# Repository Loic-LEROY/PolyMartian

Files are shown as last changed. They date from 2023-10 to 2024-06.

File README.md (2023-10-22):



## Objectives
The purpose of the robot is to carry out several tasks in complete autonomy. The tasks to be performed are as follows:
- Pick up different types of plant

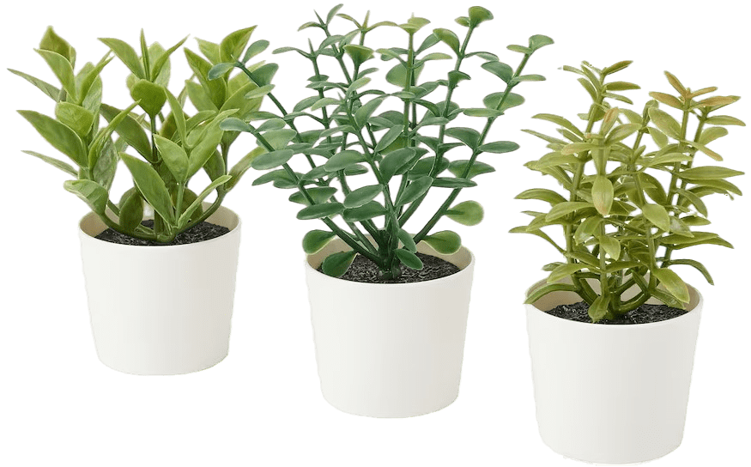
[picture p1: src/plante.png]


- Place plants in pots

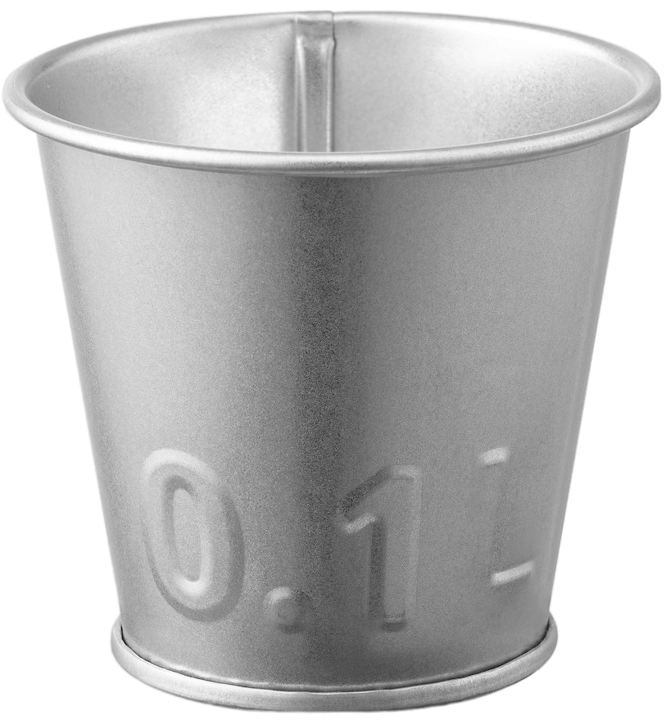
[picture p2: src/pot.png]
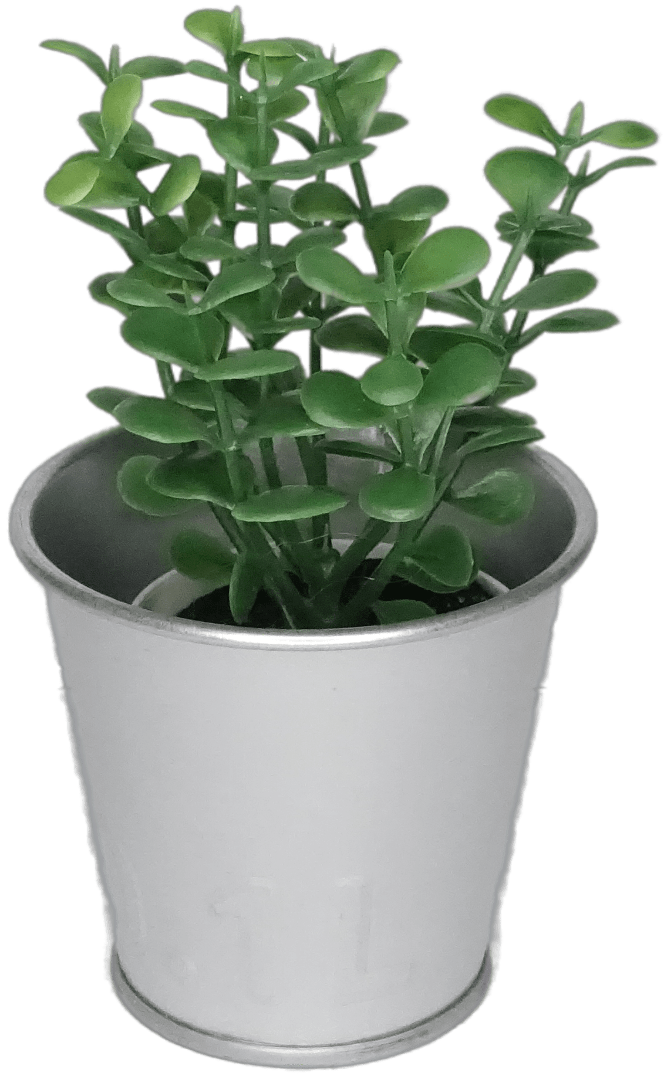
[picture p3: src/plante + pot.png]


- Bring plants to a predefined area

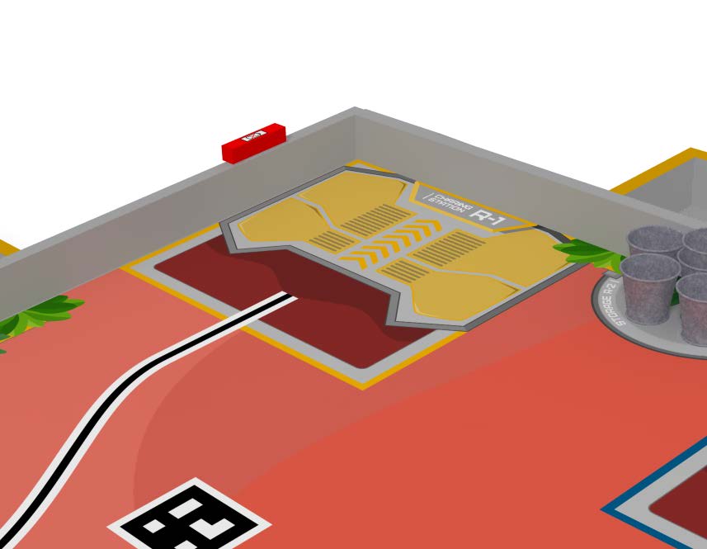
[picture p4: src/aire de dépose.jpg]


- Sort plants by type

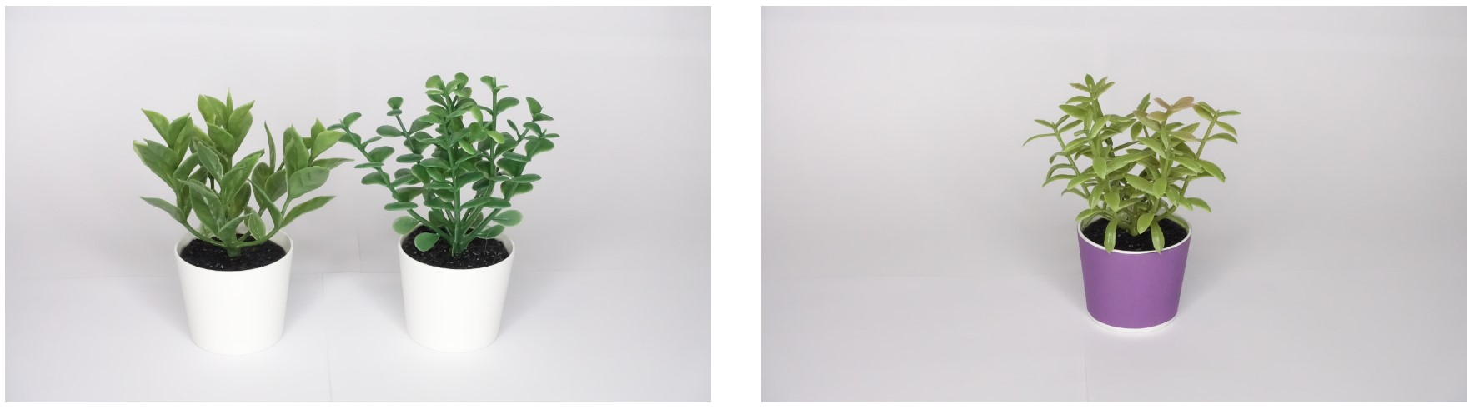
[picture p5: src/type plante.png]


> Two fragile plants, one resistant plant

- Orienting solar panels

All the work must be completed within the allotted time and without colliding with the environment (walls, other robots, plants, pots).

## constraints
- Robot dimensions :
    - Perimeter between 1200 and 1300 mm

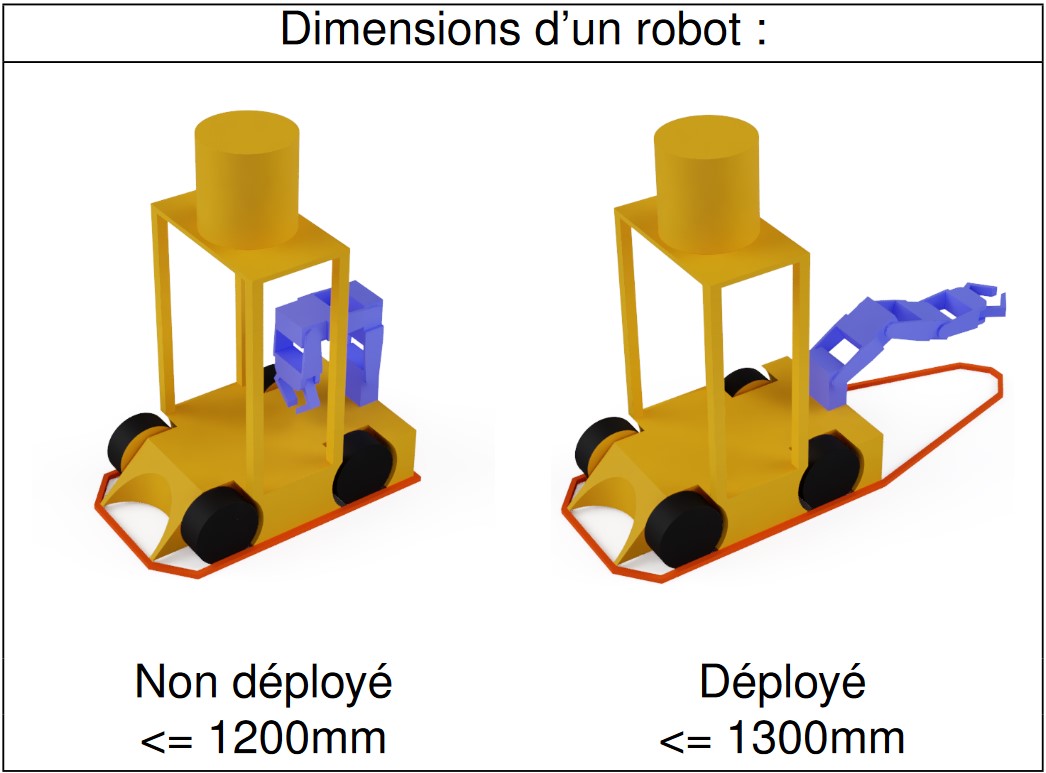
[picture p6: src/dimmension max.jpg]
    
    
    - Height under 350 mm

## Main components
- Chassis / Rolling base
- Gripper system (rail-mounted gripper)
- Vision systems (cameras, sensors)
- Storage system (turntable)

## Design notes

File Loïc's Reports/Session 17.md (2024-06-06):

# April 16, 2024
## Emergency Switch
During this session, I mounted the emergency switch to the robot. I placed it on the most accessible area possible, so that it can be easily reached in case of an emergency. I also connected the switch to the robot's power supply, so that it can cut off the power in case of an emergency. I tested the switch to make sure it works properly, and it does. The robot is now equipped with an emergency switch, which will enhance its safety features so we will be able to homologate it.



> The emergency switch mounted on the robot.

## Ultrasonic Sensors
Also, I mounted the ultrasonic sensors on the robot. I placed them on the top platform of the robot, facing forward and backward. I connected the sensors to the robot's main board, and tested them to make sure they work properly. The sensors are now ready to be used for obstacle detection and avoidance. This feature is essential for the robot to be able to participate in the competition.

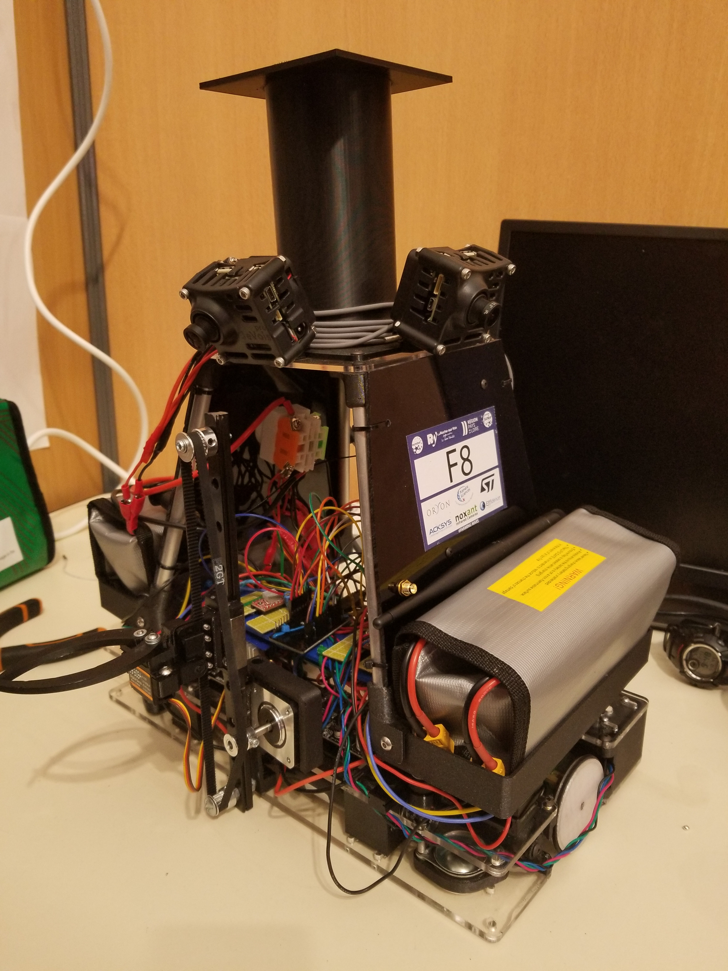
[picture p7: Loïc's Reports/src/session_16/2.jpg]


## Beacon mast
Finally, I mounted the beacon mast on the robot. I placed it on the top platform of the robot, so that it can be easily seen from a distance.



## Next session
- Participate in the competition.

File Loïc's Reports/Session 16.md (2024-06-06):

# April 09, 2024
## Cameras mouting system
To mount the cameras on the platform, I designed a mounting system that allows to easily adjust the angle of the cameras. The system is composed of a 3D printed part that can be attached to the platform using fou M4 screws. Then, a small part must be glued on the camera fan to attach it to the 3D printed part. The camera can be rotated and tilted to adjust the angle. The system is working well and the cameras are now mounted on the platform.

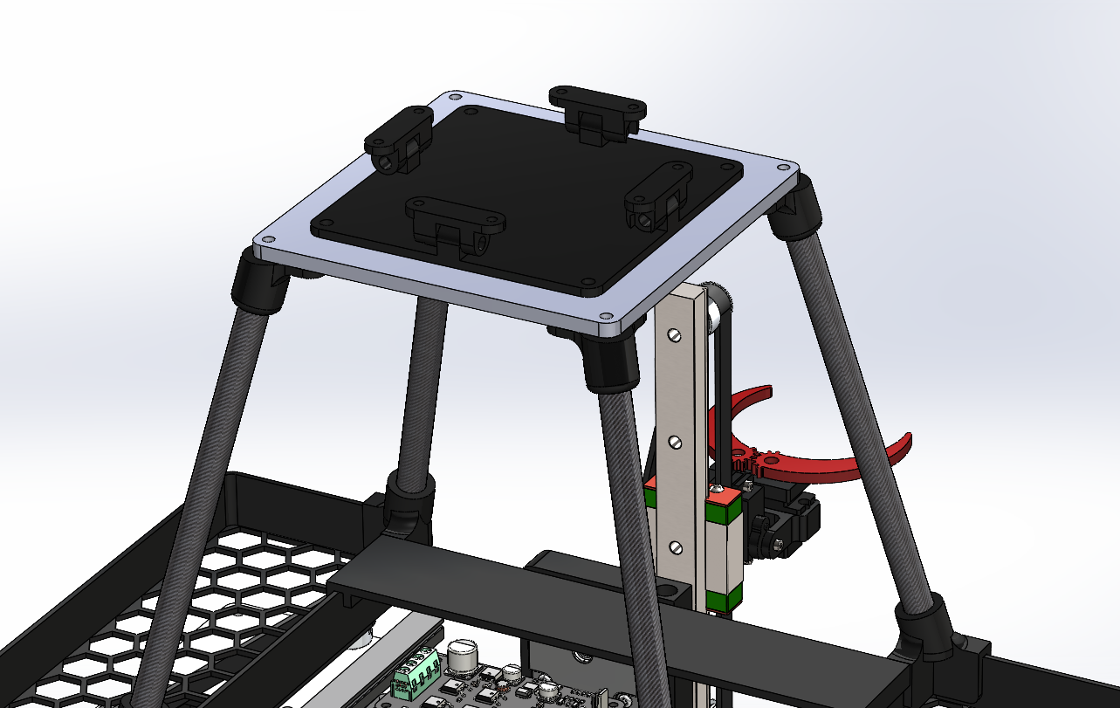
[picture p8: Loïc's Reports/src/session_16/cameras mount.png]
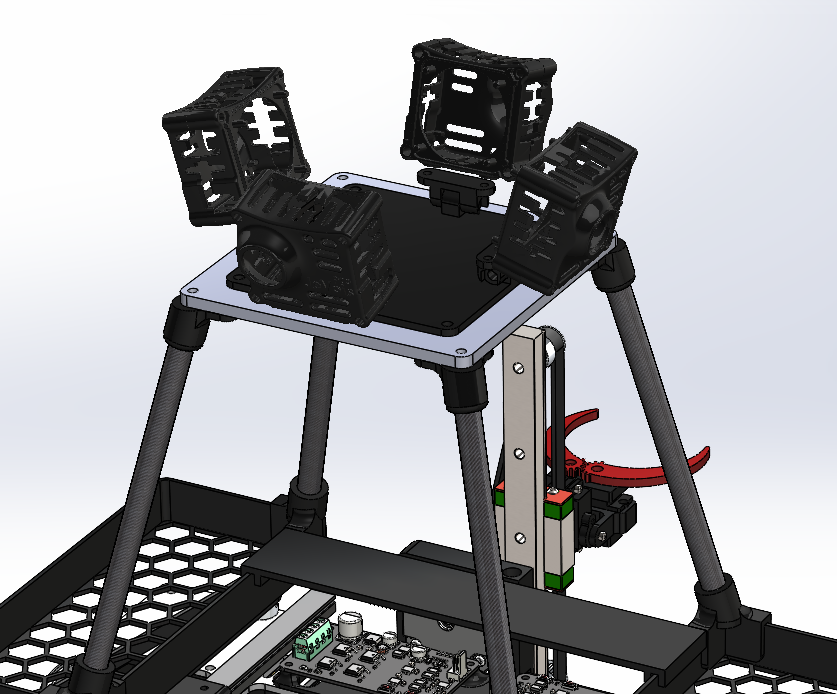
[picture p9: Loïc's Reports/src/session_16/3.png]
 

> The camera mounting system in SolidWorks



> The camera mounting system for real

## Next session
- Assemble the emergency stop button
- Design the beacon mast

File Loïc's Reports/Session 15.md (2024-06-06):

# April 02, 2024
## Cameras mounting platform
The cameras mounting platform is attached on top of the rolling base of the robot. It is composed of four aluminum tubes that are attached to the base with a 3D printed part. The platform is scarre and measures 120mm. Before laser cutting the platform itself in acrylic glass, I made one using cardboard to make sure the dimensions were correct. The platform is attached to the tubes with 3D printed parts and screws. 

<div align="center">
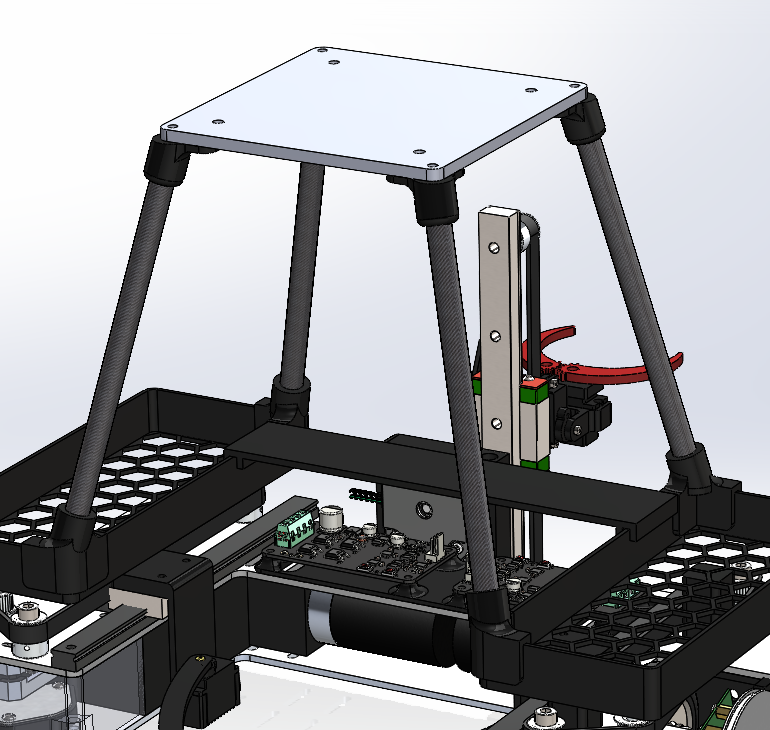
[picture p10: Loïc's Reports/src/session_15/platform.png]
    

    The platform on the robot
</div>

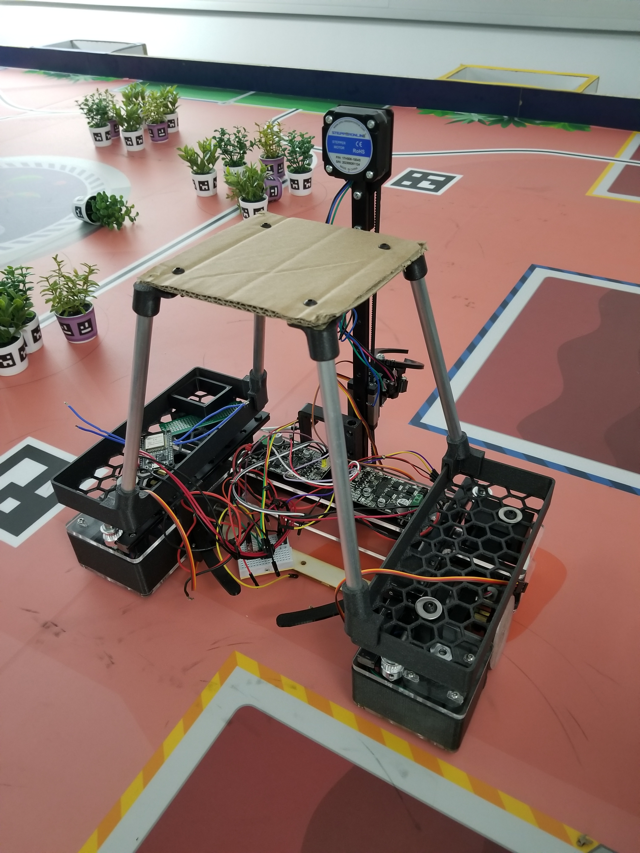
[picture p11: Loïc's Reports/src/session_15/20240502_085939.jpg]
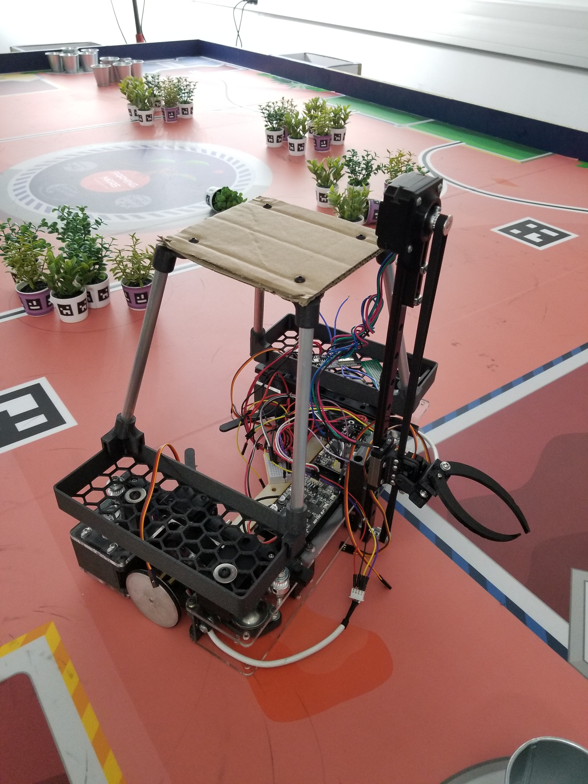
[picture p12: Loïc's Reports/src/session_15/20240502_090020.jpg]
  

> The cardborad prototype.

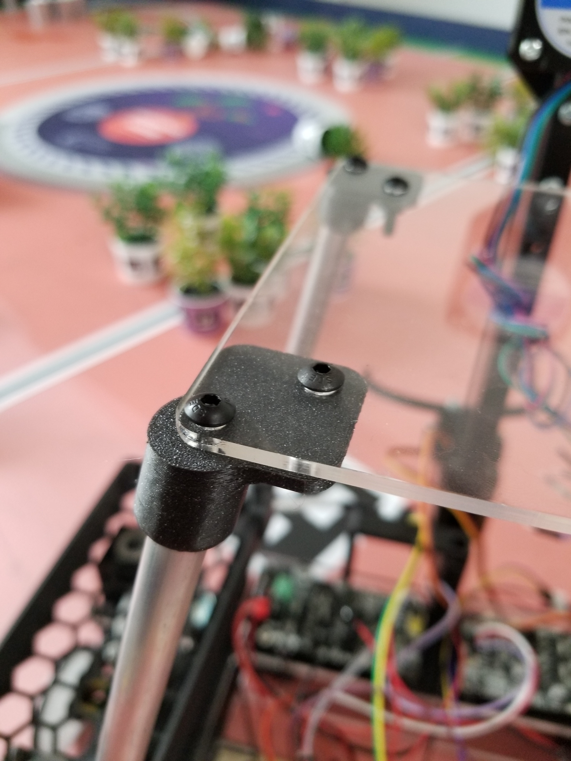
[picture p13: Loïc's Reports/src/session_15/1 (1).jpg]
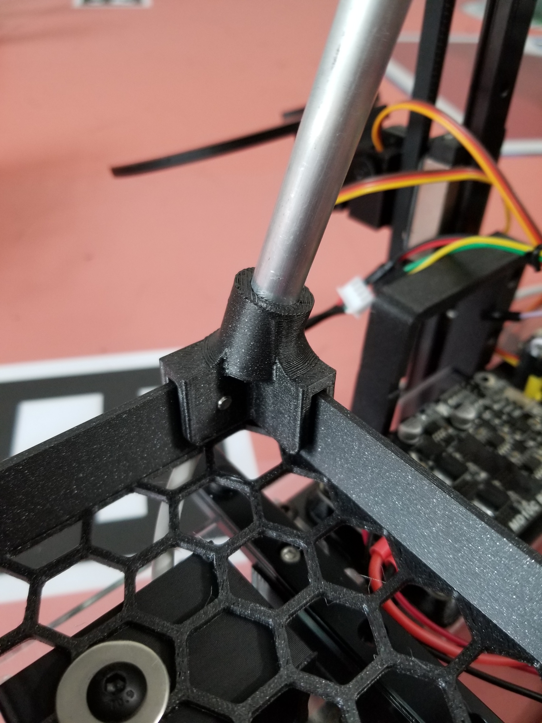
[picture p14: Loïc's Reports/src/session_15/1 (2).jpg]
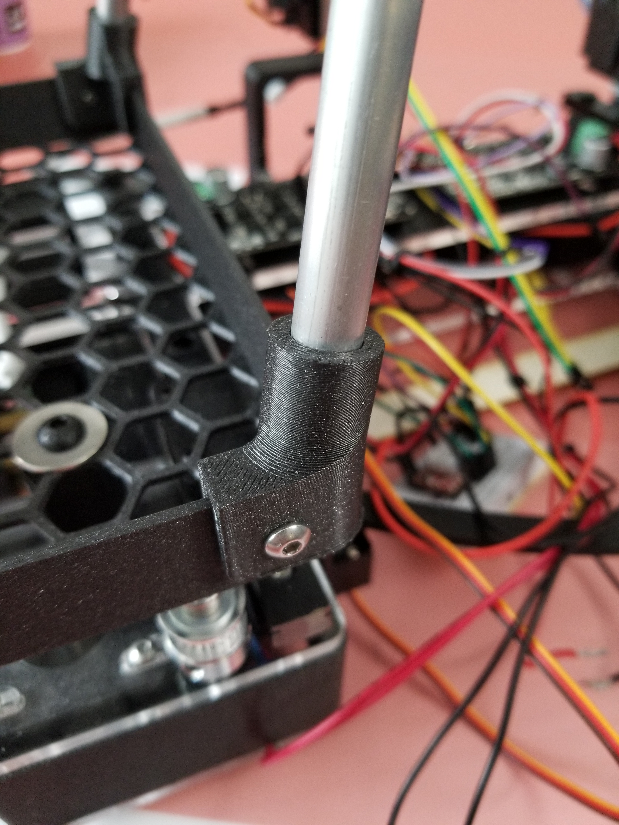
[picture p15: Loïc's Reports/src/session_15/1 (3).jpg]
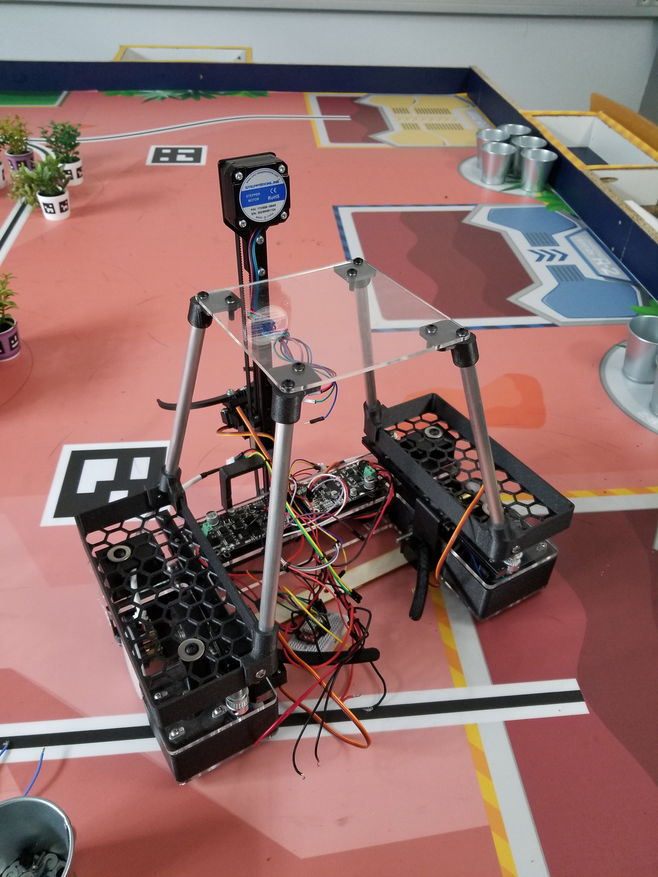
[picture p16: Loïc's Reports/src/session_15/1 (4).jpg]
   

> The 3D printed parts and the plexiglass platform.

## Next session
Next session, I will work on the cameras mounting system.

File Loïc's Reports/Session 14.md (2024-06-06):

# March 29, 2024
## Battery rack
In order to mount the batteries on the robot, I designed two "baskets" that will hold the batteries on both sides of the robot. The baskets are 3D printed in PETG for strength and durability. The bottom of the baskets have a honeycomb hole patern to lighten the weight of these parts. The batteries are held in place by a strap that goes around the battery and through the basket. The baskets are mounted on the robot using two M4 screws. Between the baskets and the robots, there are 3D printed spacers so the horizontal linear actuators can operate under them. 

On one side of the robot, the batteries are connected in series to provide 24V to it (2*3S = 24v). On the other side, only one battery is connected to provide 12V to the cameras.

<div align="center">
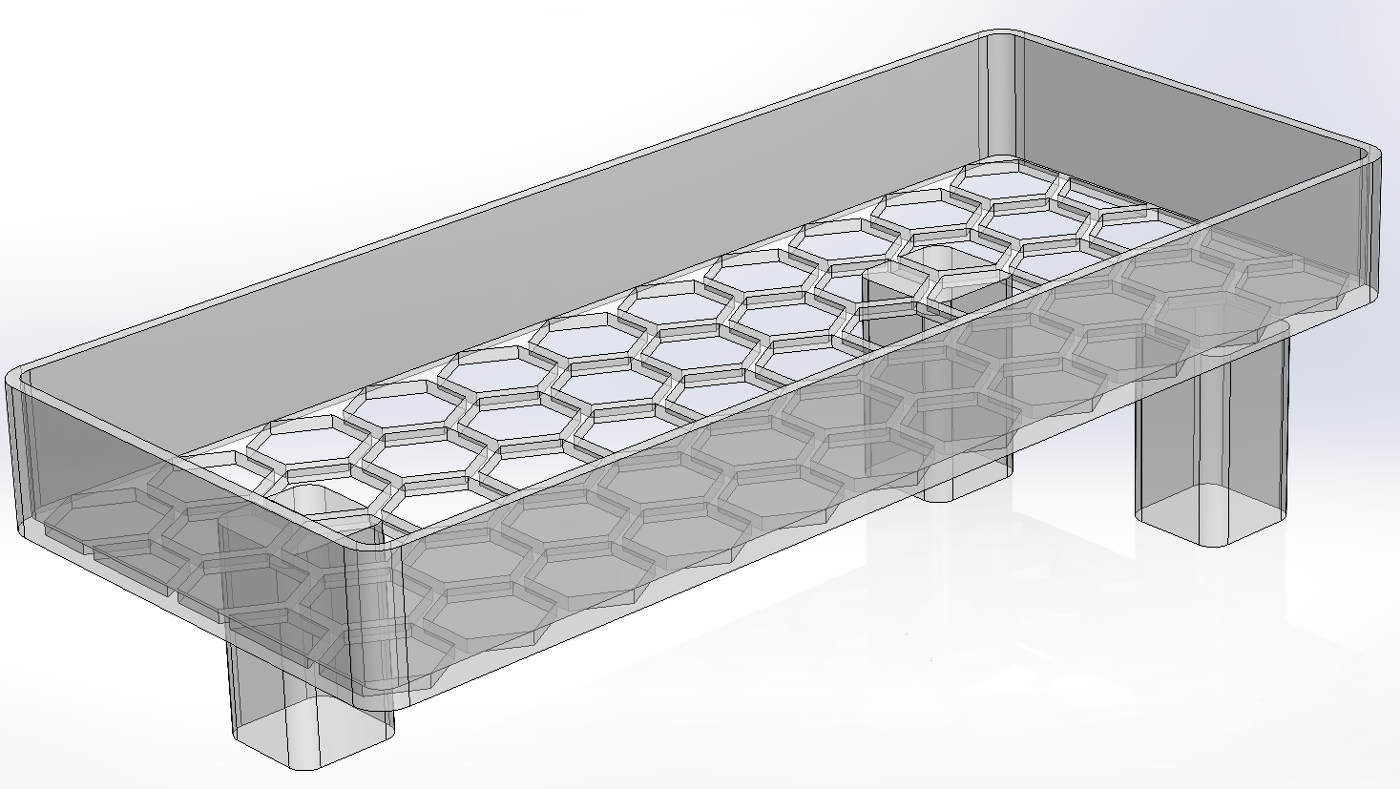
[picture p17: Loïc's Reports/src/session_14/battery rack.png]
    

    A battery rack
</div>
<div align="center">
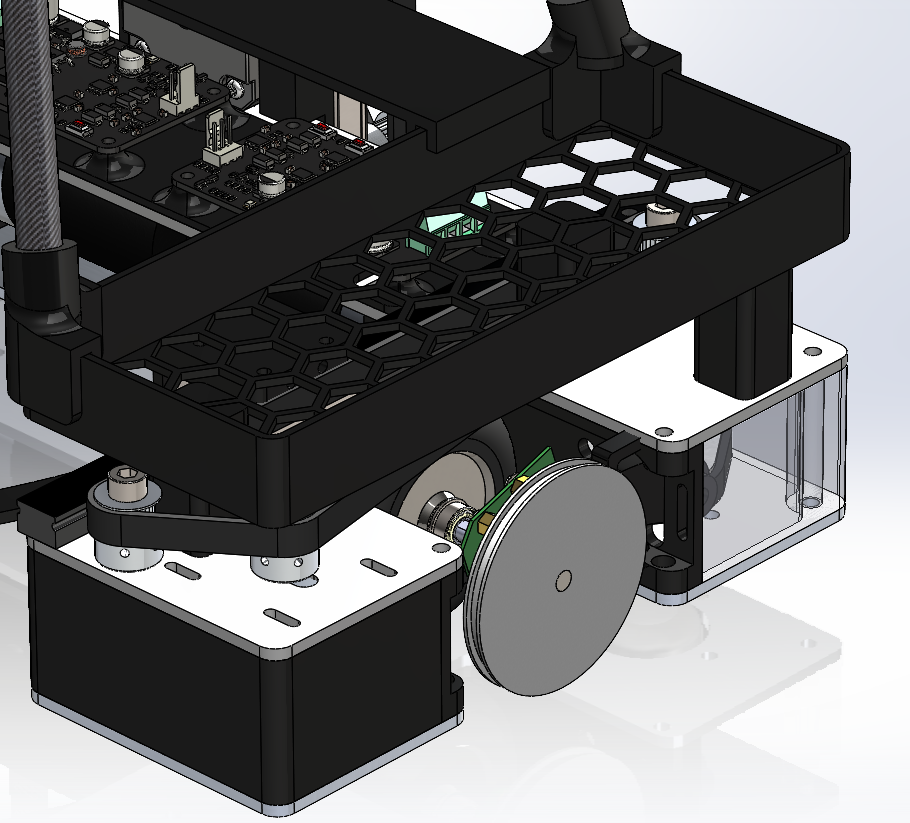
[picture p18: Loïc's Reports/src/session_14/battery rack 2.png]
    

    A mounted battery rack
</div>

## Mounting for electronics
I designed a mounting plate for the electronics that will be mounted on the robot. The plate is 3D printed in PETG. The electronics are mounted on the plate using zip ties. The plate is mounted on the robot's battries racks using super glue.

<div align="center">
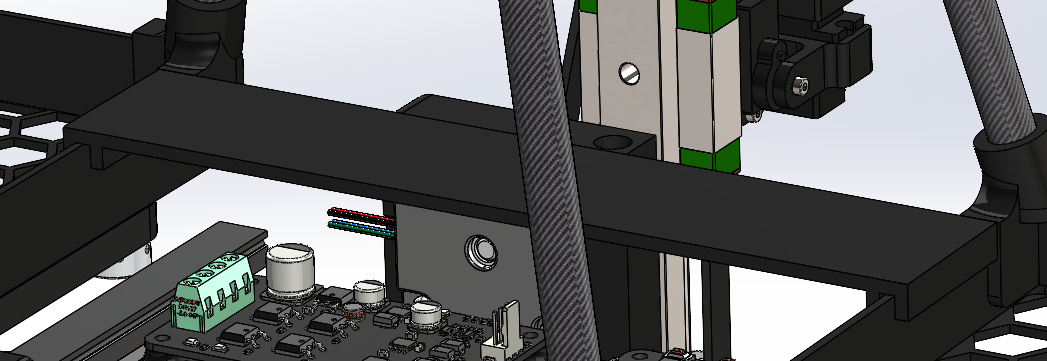
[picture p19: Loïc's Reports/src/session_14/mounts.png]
    

    Electronics mounting plate
</div>

### Next session
- Mount the electronics on the robot
- Connect the batteries to the robot
- Designed the cameras mounting system

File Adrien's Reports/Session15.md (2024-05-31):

# Session report 15: March 29, 2024

**Session objective:** Enable 2 movements trajectory to reach any coordinates on the playfield. Switch from an Arduino to an ESP32 on the robot. Find new lenses for our cameras.

## Finding new lenses for our cameras
One of the main problems at Eurobot's competition, is wifi waves interferences. So we were worried about positionning a camera on the calculation zone support, cause our communications would be easily disrupted or delayed. As our cameras are the main sensors of the robot, we decided for safety reasons to put all of  them on the robot. But the lenses provided with JevoisPro cameras have an angle near 60° so even with our 4 cameras we wouldn't be able to cover 360°.

To solve this, we decided to change our lenses for fish eyes ones which deform the image to allow huge angles sight. We chose 120° wide angle lenses to have redundancy as our cameras will be tilted towards.

## Take in hand the ESP32 chip to replace our Arduino Mega with a more powerful chip

I chosed to replace the Arduino Mega for an ESP32 for many reasons : 
- ESP32 has a higher clock speed, up to 240Mhz compared to 16 MHz for the Arduino Mega, so we will be able to have a higher sampling frequency.
- It can process to multiple tasks at the same time (for example to deploy an actuator while moving).
- It has WIFI and Bluetooth integrated, so it will be easier to send commands to configure it before making it fully autonomous.

First, we need to install the USB driver, its name can be easily identified on windows device manager and then we can downloaded from internet.
I wanted to be able to programm it with Arduino IDE, so to be able to do this, i searched for ESP32 board package by Espressif in the arduino software. 
Finally with both package and driver installed, we can easily upload code to it by selectionning the board and COM port in the Arduino menu.
Be awared that it's only possible to upload a code on it while it's in boot mode. So, to exit boot mode, on some ESP32, you need to press the boot button for few seconds while the programm is being uploaded.

## Recalibrate the robot's odometry
As a new version of the rolling base has been assembled, i had to recalibrate the odometry to be able to continue working on the displacements algorithm. To do this, i first recalibrated the robot for rotations, by reading the values from each encoder after manually doing a 360° rotation around a nail (thanks to a wood calibration part temporarily fixed on the robot which has an hole at the cinematic center of the robot). 
Ad then calibrate linear odometry by moving the robot in straight line (by pushing it forward leaning it against a wall) and reading both the values of the encoders and the distance travelled on a rule.

Linear calibration : 

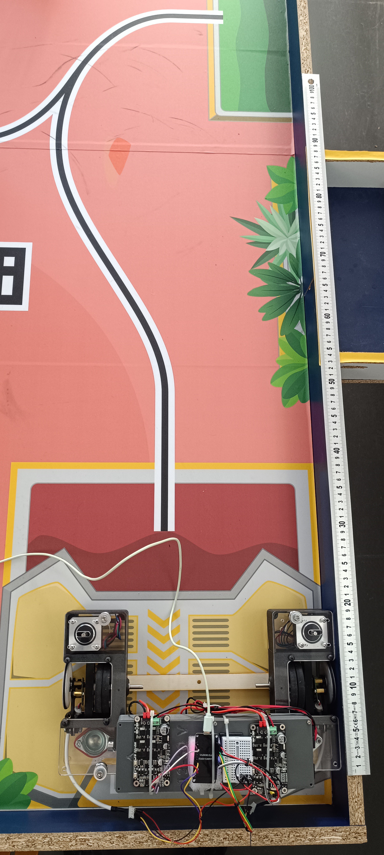
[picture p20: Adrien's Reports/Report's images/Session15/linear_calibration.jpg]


## Next session tasks
Finalize adjusting the current Arduino code to ESP32 by adding an interruption to replace millis() used for sampling. Find correct PID coefficients. Work on data transfer between ESP32 and the Jetson Nano, and between the Jetson Nano and our four cameras.

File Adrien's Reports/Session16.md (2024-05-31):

# Session report 16: April 9, 2024

**Session objective:** Switch from the Arduino Mega to an ESP32 on the robot. Etablish a connection between the Nvidia Jetson and the cameras. Optimize the closed loop control algorithm by setting a timer on the ESP32 to sample.

## Communication in USB between our cameras and the Nvidia Jetson
The first step to use our cameras on our robot was to etablish a connection between our four cameras and the Nvidia Jetson so we are able to send commands to the cameras to configure them and overall receive their processed data. As the Jetson has four usb ports, it was easier 

I then followed a tutorial written by Jevois, the manufactrer of our cameras : http://jevois.org/doc/USBserialLinux.html
To connect a camera to the Linux host provided on the Jetson using serial-over-USB, i first identified the device's port used by the camera with the command ```dmesg``` or ```lsusb```. Then i added permissions by adding my user profile to the dialout group with the command ```sudo usermod -aG dialout $USER$```. To avoid interference from the ModemManager program, which probes new serial devices, i also disabled the ModemManager  ```sudo killall ModemManager```. Then i was able to use serial communication with the application ```minicom``` (after installing it with ```pip install minicom```) and send configurations instructions to the camera.

## Problem with serial communication with ESP32
After successfully transfering a program to the ESP32, it was constantly rebooting as the following message was continously printed on the console : 

rst:0x8 (TG1WDT_SYS_RESET),boot:0x13 (SPI_FAST_FLASH_BOOT)
configsip: 0, SPIWP:0xee
clk_drv:0x00,q_drv:0x00,d_drv:0x00,cs0_drv:0x00,hd_drv:0x00,wp_drv:0x00
mode:DIO, clock div:1
load:0x3fff0030,len:1344
load:0x40078000,len:13516
load:0x40080400,len:3604
entry 0x400805f0
ets Apr 9 2024 09:22:53

After some researchs i found out that on a classic ESP32 there are 6 pins which are used by internal Flash and thus musn't be connected to anything otherwise the chip will reboot indefinitely. The problem was simply solved by switching the cables on other pins, not used by internal flash, based on the following ESP32 Pinout diagramm made by uPesy : 
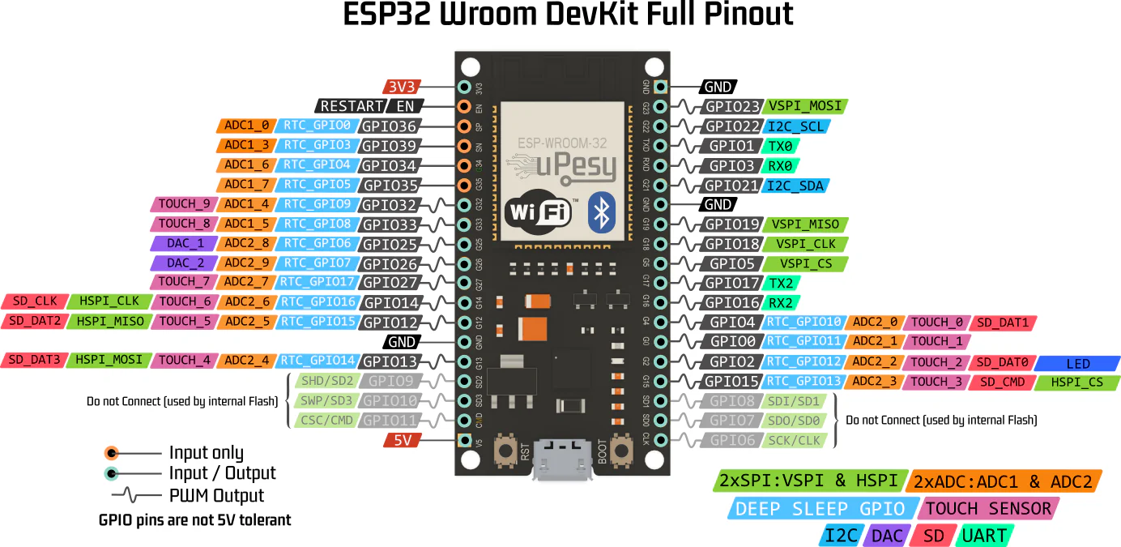
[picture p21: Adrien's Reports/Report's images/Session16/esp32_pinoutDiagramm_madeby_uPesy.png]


## Test of an encoder with ESP32
Then I wired an Encoder to the ESP32 to verify it is still working as ESP32 works only with 3.3V signals so it may be incompatible with some numerical devices if they threashold is superior at 3.3V.
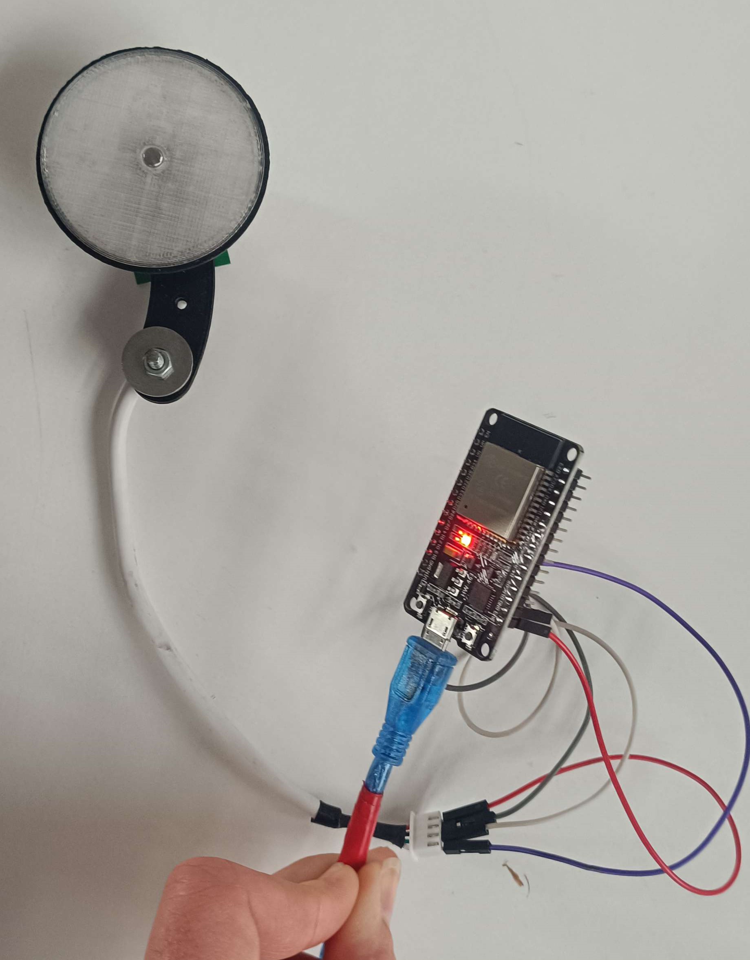
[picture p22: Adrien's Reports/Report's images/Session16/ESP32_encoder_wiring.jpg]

But hopefully communications between our encoder and the esp32 worked perfectly so it wasn't necessary to use a logic level shifting chip.

## Temporary wiring
Then i wired cables on the final version of our robot. This wiring is still temporary and will be used to do tests on the robot without waiting for all cables to be welded correctly. This will also prevent bad suprises, cause we will be sure that our wiring is correct before welding cables.

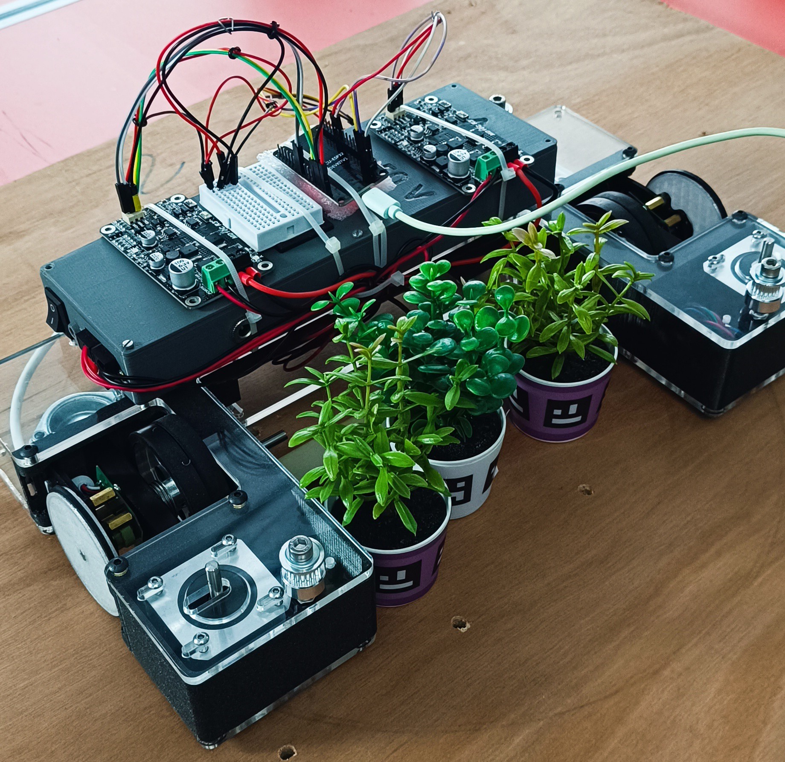
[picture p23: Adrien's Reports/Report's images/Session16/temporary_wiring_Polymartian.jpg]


## Next session tasks
We have finally received all the components to be able to assemble the final version of the robot, so next session should be fully consacred to the calibration of the PID and optimizing the robot's displacements. Finally i will implement curved trajectories which will be necessary to avoid obstacles properly without loosing too much time.

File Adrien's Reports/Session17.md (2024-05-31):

# Session report 17: April 16, 2024

**Session objective:** Create the wiring diagram of our main robot, wire cables on the final version of our robot, add programm actuators sequences.

## Wiring diagram
First, as during the competition we will probably need to do maintainance on the robot, to avoid loosing time with wiring, I created a wiring diagram on the software Fritzing. Older versions of this software can be downloaded for free here : arduinofactory.fr/telecharger-fritzing-gratuitement-et-legalement.
This diagramm will also be used by Teo Baillot, a member of the team who is in charge of the cable management of the robot and who will weld cables on the final version to avoid having cables unplugging on the robot during a match.

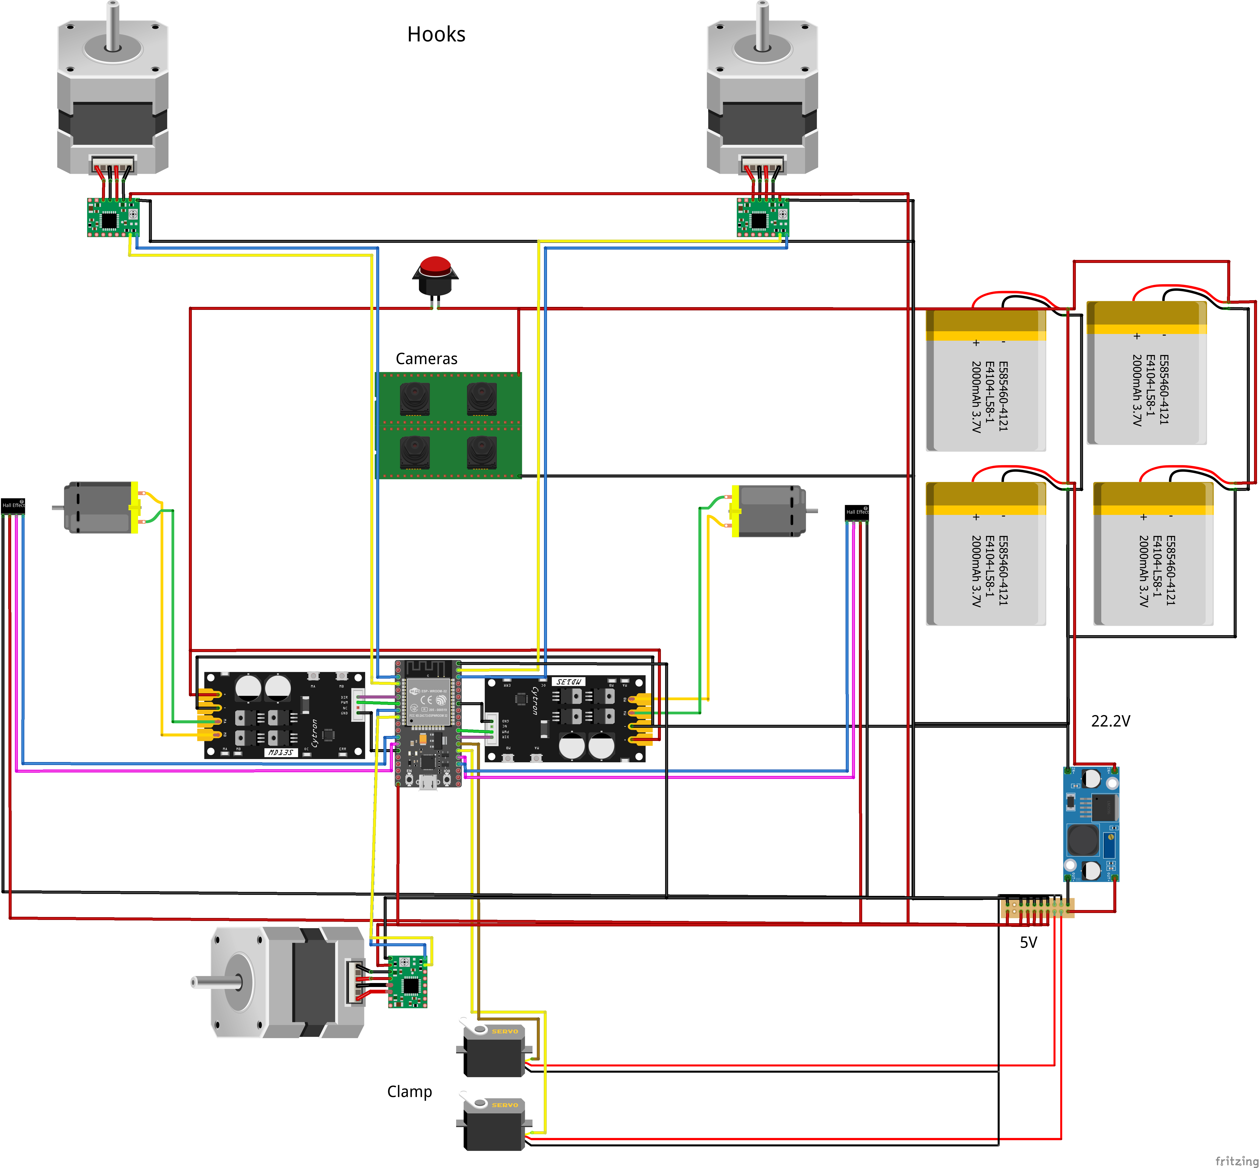
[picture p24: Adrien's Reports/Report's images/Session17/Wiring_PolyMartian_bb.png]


Two Lipos batteries are 3s 35C 2200mAh. 3S means the battery is made with 3 cells, so as each cell provides 3.7V, a 3S battery provides a voltage of 3*3.7V = 11.1V. So we put two batteries in serie to obtain a voltage around 22V which is perfect for our DC motors. 
We decided to put two more Lipos in parallel as we want to be sure that we will have enough capacity and so if we have a problem with a pair of batteries the robot will be able to continue his work with the others two batteries.

An emergency stop button is directly wired between the Lipos and the motors to be able to stop the robot at any time if a problem occurs during the competition.

## Wiring on the robot
To avoid cables disconnecting during the competition, it was indispensable to weld all cables. Even with 2 people welding cables simunlateously, it took multiple hours as the connexions on the esp32 are really thin and as we had only 0.75mm² cable. Hopefully, we made the good decision to buy silicone cables which are really convenient to weld cause they are very flexible and overall heat resistant.

But after that, we still needed to do some modifications on the robot or to modify wiring, and this experience showed us that wiring cables on a project which is aimed to be constantly modified was not the best solution. Thus, next year we will try to create our own cards with connectors for flat cables which are really convenient to disconect and reconnect and also very strong.

## ESP32 driver not foundable
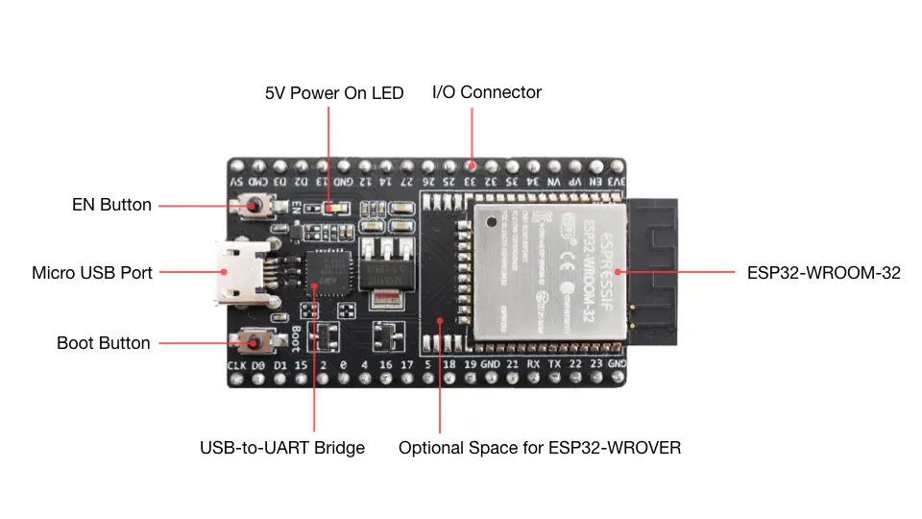
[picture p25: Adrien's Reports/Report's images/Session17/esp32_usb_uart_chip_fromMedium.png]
One of our spare ESP32 wasn't recognized by my computer. I spent almost one hour searching for this driver and testing different ones who had the same reference indicated in the device manager or also by identifying the name of the USB to serial converter chip on the ESP32 (see infography below from Medium.com) 
Our ESP32 was a copy from the original, and as i found no driver compatible with it, i wasn't able to make it work so i had to switch for another esp to not loose too much time.

## Wheel friction and weight repartition problem
Finally, now that the wiring was finished, i wanted to test the new rolling base with my closed loop control algorithm made previously but a problem occured. A wheel had too much friction compared to the other leading to bad trajectories. This was due to a free wheel which had friction with motor shaft.
The left wheel didn't grip correctly to the ground caused the inacurracy of some 3d printed part on the robot or its deformation. But this error is so small that it should be corrected when we will put weight on the robot with our batteries. Meanwhile, we can add counterweights on the robot to replace the future batteries.

## Next session tasks
Finalize the code of the robot to be ready for the robotics cup which will happen from 8th to 11th May 2024.

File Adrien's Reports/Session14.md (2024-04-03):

# Session report 14: March 29, 2024

**Session objective:** Implement new speed PID corrections where the error is the difference between the estimated speed (which is this time calculated from a trapezoidal or triangular speed profile based on the position to be reached) and the actual speed of the robot.

## Reminder

During the previous sessions, I had written a function get_phases_distance() capable of estimating the duration of each phase (acceleration, constant speed, deceleration) needed to reach a specified distance, and another function get_speed_target() capable of determining the speed target to be reached at each instant based on this speed profile.

## Resolved issue with get_speed_target()
The function worked by comparing the remaining distance to travel with the distances needed to accomplish acceleration and deceleration phases to determine when to switch to the next phase. Each time it was invoked (based on sampling frequency), it incremented the speed target by either max_acceleration or max_deceleration, depending on the current phase.

However, this approach didn't work properly because there was no correlation between the sampling frequency at which acceleration was added and the distance traveled.

To address this issue, I modified the function to be based on phase durations rather than phase distances. For instance, the duration of the acceleration phase represents the number of times we need to increment the speed target by the max_acceleration coefficient to reach the desired maximum speed. So, each time get_speed_target() is called, I increment a time variable by one, representing the number of times max_acceleration has been added to the target speed and when this variable reaches the acceleration time calculated by the get_phases_distances() function, the system can switch to the constant speed phase.

## Adapting get_speed_target() for different speeds on each wheel
To enable the use of get_speed_target() for rotation or reverse movement, I've introduced two coefficients, one for each wheel. These coefficients are multiplied by the final speed target to yield a rotation speed for each wheel. Consequently, if the left coefficient is set to -1 and the right coefficient to 1, the robot will pivot in place.

## Calculating error
Calculating the error was quite tricky as we now have two errors: one for linear speed and the other for angular speed. Additionally, we have the integrals of these variables, which represent linear position and angular position.

To make it easier to understand, I decomposed the problem into three functions:

1) get_theorical_speed_and_position()
2) get_real_speed_and_position()
   
These two functions will be used to dermine 5 parameters :
The linear velocity of the robot :
$$V = leftSpeed + rightSpeed $$ 

Its angular velocity :
$$W = rightSpeedTarget - leftSpeedTarget$$ 

Its angle travelled (integral of the angular velocity) : 
$$Z = previousZ + W $$ 

Distance travelled on x axis (integral of x component of linear speed) :
$$X = previousX + V * cos(Z)$$ 

Distance travelled on y axis :
$$Y = previousY + V * sin(Z)$$ 

The difference between the two functions is that the first one will process these operations with theoretical values, which are determined relative to the speed profile, while the second one will process with real speeds determined using the encoders.

3) get_errors() which calls the two functions above to process the errors calculus (difference between theorical speed/position and real speed/position).
$$ errorDistance = \sqrt{( (Xtheorical - Xreal)² + (Ytheorical - Yreal)²} ) $$ euclidean norm to determine the distance between the points (Xtheorical, Ytheorical) and (Xreal, Yreal).

$$ errorAngle = atan2(Ytheorical - Yreal, Xtheorical - Xreal) - Zreal $$ trigonometric relation where atan2 is a mathematical function which processes to arctan of the first paramater divided by the second one.

These two variables are used to calculate the errors we will use in our pid correction : 
$$ errorXY = errorDistance * cos(errorAngle) $$
$$ errorV = Vtheorical - Vreal  $$
$$ errorZ = Ztheorical - Zreal $$
$$ errorW = Wtheorical - Wreal $$

## Implementing the PID correction and send command to motors
Finally we are now able to create a function that will apply Proportional, Integral (and eventually Derivation if needed later) coefficients to our errors to send the resulting command to the motors. Of course we need two differents PID, one for linear speed : errorV and the other one for angular speed : errorW.

$$ pid_v = P_V * errorV +  I_V * errorXY $$
$$ pid_w = P_W * errorW +  I_W * errorZ $$

The resulting motors command are then : 
$$ LeftCommand = pid_v - pid_w $$
$$ RightCommand = pid_v + pid_w $$

## Next session tasks
- During next session, Loic will assemble the final version of the rolling base so after that i will have to recalibrate the robot and find the correct PID coefficients to verify everything is working correctly.
- Work on a way to send the data processed by our cameras to the Jetson.

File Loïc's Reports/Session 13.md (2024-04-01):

# March 19, 2024
## Ladybug
### Components
#### Ultrasonic sensors and camera
Last session, I ended up with this for the chassis of the Ladybug :

<div align="center">
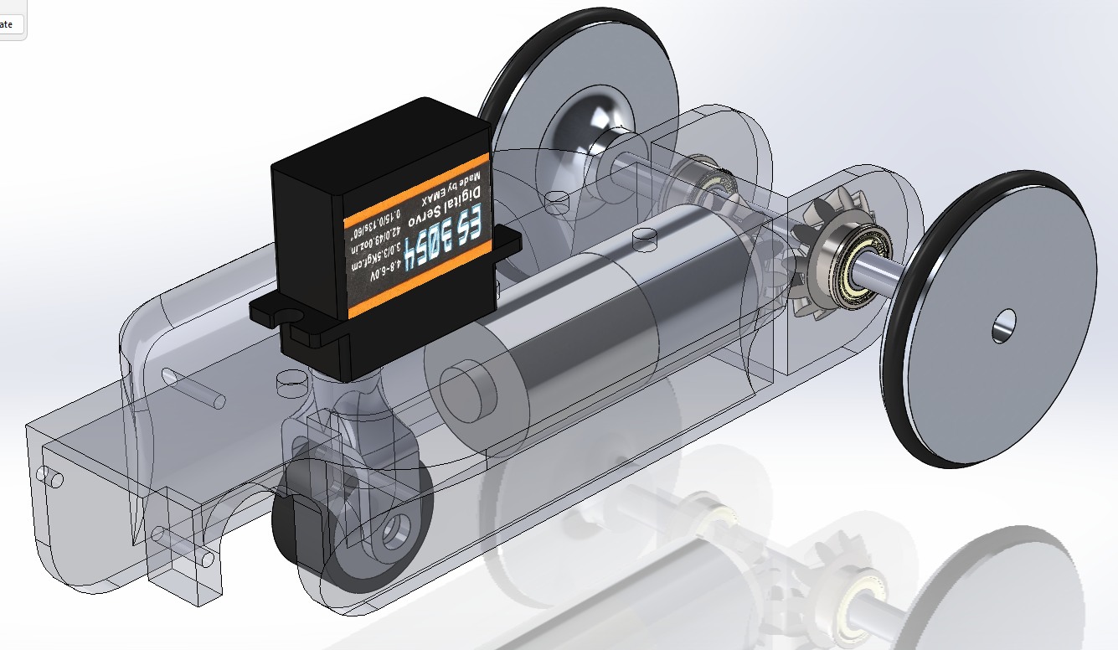
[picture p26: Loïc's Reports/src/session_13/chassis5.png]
    

    Chassis of the Ladybug
</div>

Today, I will continue to work on how the sensors will be placed on the chassis. I will start with the ultrasonic sensors and the camera. Because I want the robot to be as compact and as light as possible, I had the idea to use the servo motor as a support for the sensors. This way, I can use a small piece to attach the sensor to the servo. The bracket clips onto the servo motor. Here is the result :

<div align="center">
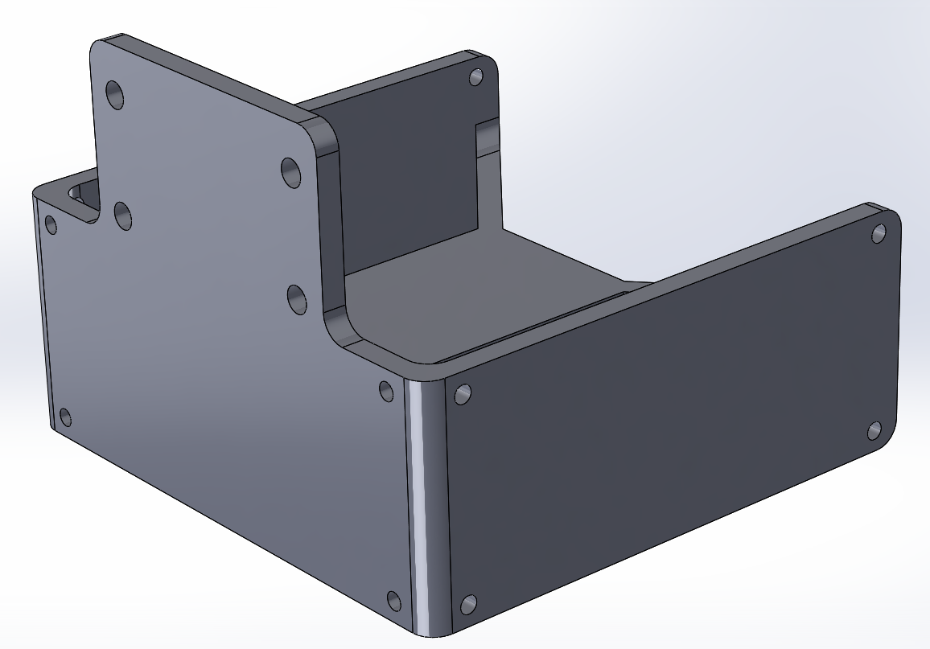
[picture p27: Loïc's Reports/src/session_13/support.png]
    

    The support for the sensors (Front view)
</div>
<div align="center">
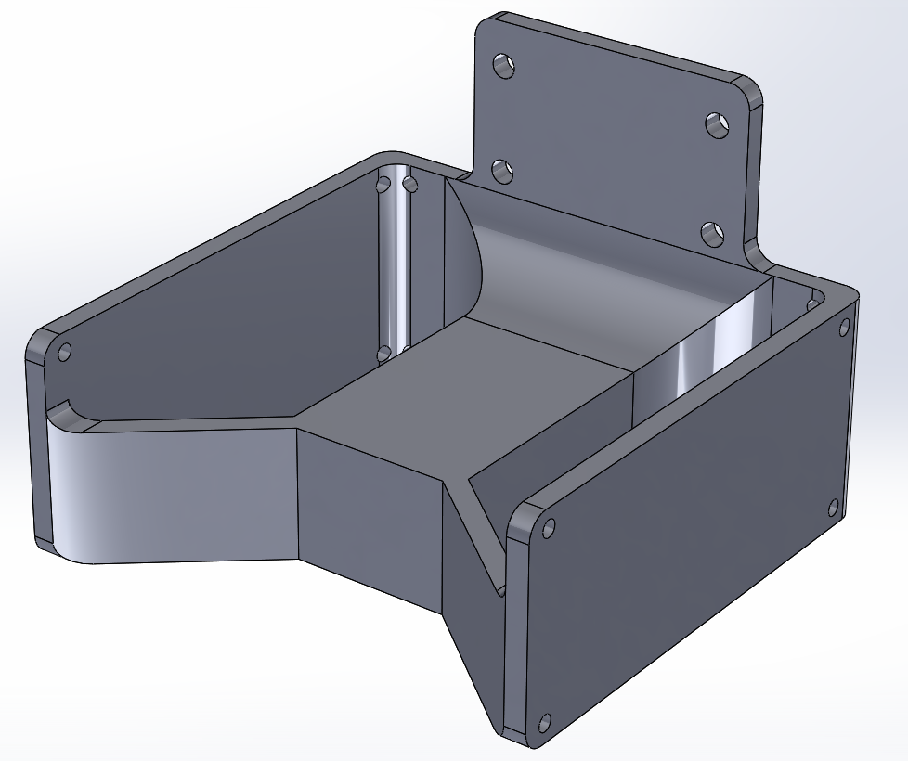
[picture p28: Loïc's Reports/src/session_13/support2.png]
    

    The support for the sensors (Back view)
</div>
<div align="center">
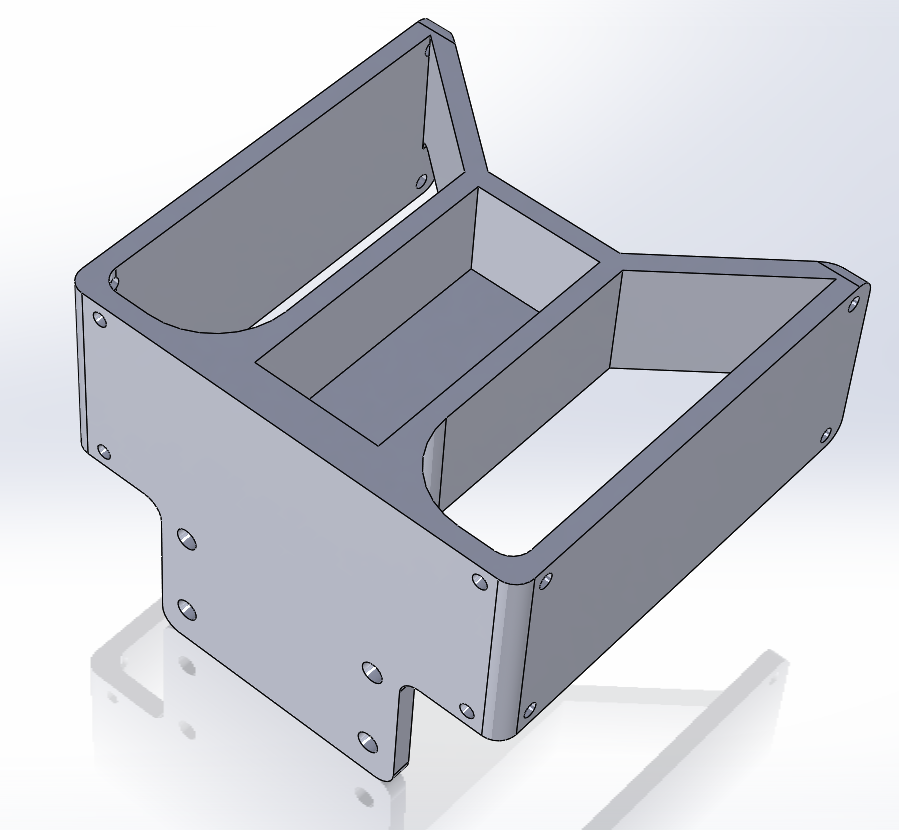
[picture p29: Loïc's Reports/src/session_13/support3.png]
    

    The support for the sensors (Bottom view)
</div>
<div align="center">
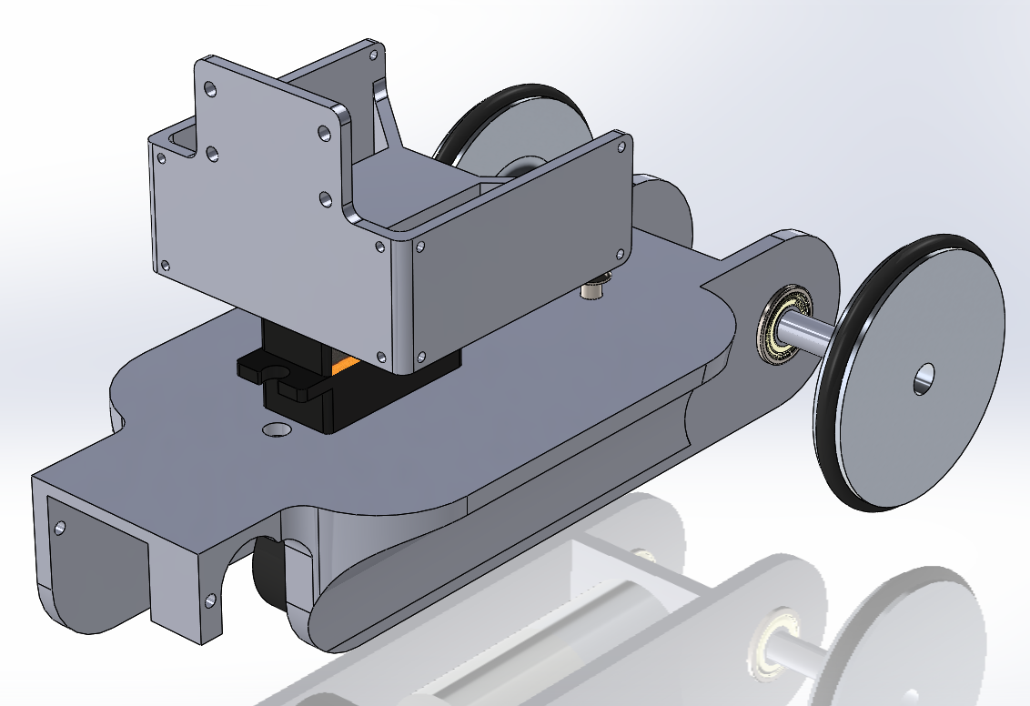
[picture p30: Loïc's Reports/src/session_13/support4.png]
    

    The support for the sensors mounted on the servo motor
</div>

Now, I can screw the ultrasonic sensor and the camera on the support.

<div align="center">
    

    The ultrasonic sensors and the camera mounted on the support
</div>

#### Battery, Raspberry Pi pico W and BMS
The rest of the components are directly placed on the chassis.

<div align="center">
    

    The battery, the Raspberry Pi pico W, the BMS (Battery Management System) on the chassis (Front view)
</div>
<div align="center">
    

    The battery, the Raspberry Pi pico W, the BMS (Battery Management System) on the chassis (Back view)
</div>

#### DWM1001-DEV module
The DWM1001-DEV module is a bit particular because it has to be placed on the top of the robot, in the center, **vertically**. I had to design a specific support for it which is screwed on the chassis. The support is very simple, it is just an extruded T shape, held by to screws to the chassis. Here is the result :

<div align="center">
    

    The support for the DWM1001-DEV module
</div>
<div align="center">
    

    The support for the DWM1001-DEV module mounted on the chassis
</div>
<div align="center">
    

    The DWM1001-DEV module mounted on the support
</div>

### Actuator
The goal of the ladybug is to pollinate the plants we placed with the main robot. According to the rules of the competition, a plant is pollinated when the ladybug touches it. To do so, I will use a small servo motor to move a kind of arm. The arm will be placed on the front of the robot. Here is the result :

<div align="center">
    

    The servo motor placed under the ladybug in the chassis
</div>
<div align="center">
    

    The arm of the actuator mounted on the servo motor
</div>
<div align="center">
    

    The actuator (Front view)
</div>

### Emergency stop button
The last component I had to place on the chassis is the emergency stop button. I placed it on the top of the robot, between the ultrasonic sensors so it is very accessible by the referee in case of emergency. Here is the result :

<div align="center">
    

    The emergency stop button mounted on the chassis
</div>

### Fabrication
Now that the ladybug is fully designed, I can start the fabrication. All the grey parts on the pictures above will be 3D printed because this process is quick and easy. 3D printing also has the advantage of being quite precise, afordable compared to CNC machining and it allows to create complex shapes (like the chassis). Because my design is experimental, 3D printing is the best option to test and iterate quickly.

## Next session
- Print the parts
- Adjust some parts of the main robot

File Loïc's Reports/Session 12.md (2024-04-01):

# March 12, 2024
## Main robot
Two session ago, I modeled and printed the system which will hold the plants against the robot's frame. when I tried to mount them on the robot, I realized that the system was a little bit too long. I had to cut it and reassemble it. The difficulty was to cut the guide rail because it is made out of hardened steel so it cannot be cutted with a regular steel saw. Finally I found out that a [Dremel®]('https://www.dremel.com/fr/fr/p/dremel-8260-f0138260ja') with the right blade was able to cut through it whithout too much difficulties.

<div align="center">
    

    Cutted rail guide
</div>

## Ladybug robot
### Components
Last session, I chose the components for the ladybug robot. Before starting to model the ladybug itself, I modeled on SolidWorks the components that will be used in the robot. I modeled the DC motor, the servo motors and the DWM1001 module. I found the other components on the internet because they are standard. Here are the components I modeled myself on SolidWorks:

<div align="center">
    DC motor

    DC motor
</div>
<div align="center">
    Servo motor

    Servo motor (for the direction)
</div>
<div align="center">
    Servo motor

    Servo motor (for the actuator), a bit smaller than the previous one
</div>
<div align="center">
    Servo motor

    DWM1001 module
</div>

Here are the components I found on the internet ([GrabCAD]('https://grabcad.com/library')):
<div align="center">
    Servo motor

    Ultrasonic sensor
</div>
<div align="center">
    Servo motor

    Raspberry Pi camera
</div>
<div align="center">
    Servo motor

    18650 battery in a holder
</div>
<div align="center">
    Servo motor

    BMS (Battery Management System) for the 18650 battery and step-up module (3.7V to 5V)
</div>
<div align="center">
    Servo motor

    Raspberry Pi Zero W
</div>
<div align="center">
    Servo motor

    Emergency stop switch
</div>

### Chassis
For the chassis, I modeled it as compact and simple as possible. I designed it so that the DC motor is inside the chassis, so that its mass serves to stabilize the ladybug. The structure of the chassis is very rigid because of its geometry, when can see some holes on the top which are made to screw the other parts on it. Here is the design I came up with:

<div align="center">
    Chassis

    Chassis (Top view)
</div>
<div align="center">
    Chassis

    Chassis (Bottom view)
</div>
<div align="center">
    Chassis

    Chassis (front view)
</div>

Then I added to the chassis the DC motor, the servo motor for the direction and the wheels. A small wheel is mounted on a fork which is attached to the servo motor. In order to transmit the rotational power from the DC motor to the wheels, I designed a small gear system. The gear ratio is 1:1, so the wheels will rotate at the same speed as the DC motor which is already designed at the right speed. The wheels might be a little bit too much apart but I will see this detail later. Here is the chassis with the motors and the wheels:

<div align="center">
    Chassis

    Chassis with the DC motor, the servo motor and the wheels (Bottom view)
</div>
<div align="center">
    Chassis

    Chassis with the DC motor, the servo motor and the wheels (Top view)
</div>

## Next session
- Continue the ladybug robot
- Adjust some parts of the main robot

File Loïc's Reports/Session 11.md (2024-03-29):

# March 05, 2024
## Ladybug
During this session, I started to work on the Ladybug (mini robots) which will be used to "polenize" the plants. The robots will have to complete this task only during the last 10 seconds of the match. The task is complete if a ladybug touches a plant at the end of the game. Each ladybug will have to be able to move in all directions and to detect the plants. The ladybugs have to be as simple as possible so they are easy to build, easy to program and easy to repair. While moving, a ladybug must avoid any obstacle.

### Motorisation
For the main motor (for the wheels), I chose the 12V DC motor. It is a simple motor that can be powered by a battery. It is also easy to control with PWM and a H-bridge. Because I don't want the robot to be too fast, I will run this motor at 5v and I chose a motor with a planetary gearbox to reduce the speed in a minimum of space.

<div align="center">
    

    The motoreducers
</div>

### Motherboard
For the main board, I chose the Raspberry Pi Zero W. It is a small and cheap board with a lot of GPIOs. It also has a camera port which will be useful to detect the plants. The Raspberry Pi Zero W is also powerful enough to run a simple AI to avoid obstacles. The Raspberry Pi Zero W will be powered by a 5V battery and will control the motors with a H-bridge. The Wifi will be used to communicate with the main computer and receive and send its position.

<div align="center">
    
    

    Raspberry Pi Zero W pinout and the four Raspberry Pi Zero W
</div>

### Camera
For the camera, I chose the Raspberry Pi Camera Module V2. It is a small camera that can be connected to the Raspberry Pi Zero W. It is also cheap and easy to use. The camera will be used to detect the plants and to avoid obstacles.

<div align="center">
    

    Camera Module V2
</div>

### Actuators
For the actuators, I chose a servo motor ES-3054 because it is compact, strong and durable (metal gears). I prefer servo motor for my application because it is super easy to control (self-servoed). I will use a servo motor to move the directive wheel and and one to move the arm that will touch the plant.

<div align="center">
    
    

    ES-3054 servo motor
</div>

### Battery
For the battery, I chose the 3.7V 1500mAh Li-ion battery. It is a small and light battery that can be recharged. It is also powerful enough to power the Raspberry Pi Zero W and the motors. I will use a step-up to power the Raspberry Pi Zero W with 5V. The battery will also be equipped with a protection circuit to avoid over-discharge and over-charge which can be dangerous (explosion in the worst case). The battery cell will be protected in a Power Bank case to make it easy to recharge and certified for the competition. Without the case, I would have to keep it in a fireproof bag which is not practical.

<div align="center">
    
    

    18650 Li-ion battery cell
</div>

### Emergency switch
For the competition, I have to add an emergency switch to stop the robot in case of a problem. I chose a simple switch that will cut the power of the robot. The switch will be placed on the top of the robot to be easily accessible.

<div align="center">
    

    Emergency switch
</div>

### Sensor
For the sensors, I chose the HC-SR04. It is a small and cheap ultrasonic sensor that can measure the distance with enough precision. The sensor will be used to detect obstacles on the front and the sides of the robot. The sensor will be placed in the center top of the robot to have a good view of the environment.

<div align="center">
    

    HC-SR04 ultrasonic sensor
</div>

For the robot to know its position on the field, I will use a DWM1001-dev module. The module can be used to know the position of the robot with a precision of 5 to 10 cm which is enough. The module will be placed on the top of the robot to have better performance. According to the datasheet, it is better to place the module vertically. The module will communicate with the Raspberry Pi Zero W with UART.

<div align="center">
    

    DWM1001-dev module
</div>

## Next session
- Design the ladybug with the selected components on SolidWorks
- Adjust some parts of the main robot

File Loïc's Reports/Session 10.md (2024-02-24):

# February 21, 2024
## Horyzontal guiding system
During this session, I modeled the horyzontal guiding system. I used the same method as for the vertical guiding system : 
- A horyzontal linear guide
- A horyzontal carriage
- A stepper motor to move the belt arround the pulley (not shown on the picture below)
- A belt to connect the stepper motor to the carriage

On the carriage, There is a part to hold the servo motor which will open and close a claw to prevent plants to fall when the robot is moving. The stepper motor on the right of the image below is mounted upside down to make the rest of the system more compact. The part which holds the stepper motor has a hole to let the belt pass through it as well as the guide.

<figure align="center">
    
    
    
</figure>

> The horyzontal guiding system

Here are the steps the robot will do to move the plants from one place to another:
1. The robot arrive to one of the plants spot
2. The robot opens the claws
3. The robot moves forward to the plants until it surrounds them
4. The robot closes the claws
5. The robot moves slides the claws from the front to the back to make sure the plants are well held against the robot's frame
6. The robot moves to the other spot

To unload the plants, the robot will do the same steps but in reverse order.

I didn't had time to mount these parts on the robot but I will do it during the next session. Here are the printed parts:

<figure align="center">
    
</figure>

## Next session
- Mount the printed parts on the robot
- Design the ladybugs
- Design the system to move the solar panels

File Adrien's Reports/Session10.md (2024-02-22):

# Session report 10: February 22, 2024

**Session objective:** Take our PID to the next level by avoiding common imperfections and delve into using our cameras for shape recognition.

The PID algorithm created during the previous sessions was functional, but occasionally exhibited erratic behavior. To enhance it, I sought assistance from the excellent article 'Améliorer vos régulateurs PID' by the PM-Robotic team and the fantastic series of tutorials 'PID control' from the Matlab YouTube channel.

## Establish a proportional relationship between sample time and P, I, D coefficients.

"First of all, the initial issue was that I had established no link in my code between my P, I, D coefficients, and the sample time. So, even when I changed the sample time, I was still integrating and differentiating the error over the same time period. To avoid the need to adapt I and D correction coefficients after each modification of the sample time, I multiply my integral coefficient I at the beginning of the program by the sample time because we integrate error*dt. Similarly, I divide my derivative coefficient D by the sample time because we want to differentiate ${derror \over dt}$, where dt is the short period of time over which we are performing the operation.

## Avoid derivative kick

As our error is calculated as follows: Error = DistanceSetpoint - DistanceTravelled, if we change DistanceSetpoint, the error will change so rapidly that its derivative will tend toward infinity. This will create an undesired spike in the calculated output when applying the PID correction.



Source : PM Robotix team

One solution is called 'Derivative on Measurement'; I explain it in the context of my algorithm:

Error = DistanceSetpoint - DistanceTravelled

So its derivative is equal to:
\[ \frac{dError}{dt} = \frac{dDistanceSetpoint}{dt} - \frac{dDistanceTravelled}{dt} \]

However, DistanceSetpoint is the distance instruction, so it remains constant until a new instruction is sent. Consequently, its derivative is equal to zero. This leads to the following result:
\[ \frac{dError}{dt} = - \frac{dDistanceTravelled}{dt} \]

Now that our derivative is no longer directly dependent on the Setpoint, we avoid high-speed changes and prevent spikes in output when the setpoint changes.

## Changing PID coefficients in real time
To determine P, I, D coefficients, it can be really helpful to be able to modify our coefficients in real-time to visualize the evolution and influence of our modifications on the error. It's a great time-saver because it avoids restarting the program for each modification.

However, there is a significant problem to be aware of. Instantly modifying the integral coefficient can create a bump in the output. When we multiply the I coefficient by the integration of the error, I coefficient is assumed to be constant. But this assumption is no longer valid if we modify it while the program is running. To solve this, we can simply include the I coefficient inside the integral. Now, I sum I×errorI×error to the integral term each time the output is corrected, rather than adding the error to the sum and multiplying it by I later.

## Reset Windup
This is one of the most frequent problems in PID implementation. Our system is not perfect because our motors are speed-limited. If we attempt to exceed this limit, our motors will saturate at their maximum speed, causing our system to become nonlinear. However, the main issue is that our integral term will continue to grow, assuming the motor speed is still increasing to correct the error faster. Finally, when our value drops below the saturation point, the integral term will be excessively high and unrelated to the actual error. As a result, the robot will deviate significantly from its setpoint.

This problem is well-explained further in Matlab videos: Understanding PID Control Part 2: Expanding Beyond a Simple Integral."

To address this issue, the integral term is now increased only when there is no saturation, indicating that our motors are not operating at their maximum speed. In cases of saturation, correction is applied using only a proportional coefficient.

## Set up our JeVois Pro camera for shapes recognition

The main reason we chose these specific cameras is their integration of powerful chips, enabling us to process calculations directly from the camera and then transmit the results to our Nvidia Jetson Nano. This approach allows us to leverage the computational power on the Jetson Nano for real-time strategy elaboration with artificial intelligence.

Getting acquainted with the camera was straightforward, as many programs come preinstalled on the camera chip with the Ubuntu operating system. After adjusting the focal length using the small wheel around the lens, I tested programs to recognize objects and Aruco markers.



The provided software is highly comprehensive, allowing us to adjust camera settings and customize preinstalled programs based on our specific conditions, including parameters such as the size of our Aruco markers.

I achieved excellent results directly, as showcased in the following videos:

Plants detection: https://youtube.com/shorts/sOcyxpt3ze8
Aruco detection: https://youtube.com/shorts/fuHYHDNQBM0

This will significantly save us time, as we can use this algorithm to extract data from the cameras and transmit them to the Jetson, with just a need for some adaptations to fit our specific use.

## **Next session tasks:**
In the upcoming session, the PID correction will be fully implemented and configured, along with our odometry. I will focus on developing obstacle avoidance paths and establishing a method to transmit the output from our cameras to our main Nvidia Jetson Nano. This data will be utilized to inform decision-making strategies with artificial intelligence.

## Sources :
https://www.pm-robotix.eu/2022/02/02/asservissement-et-pilotage-de-robot-autonome/

https://fr.mathworks.com/videos/understanding-pid-control-part-1-what-is-pid-control--1527089264373.html

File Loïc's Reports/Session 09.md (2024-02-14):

# February 14, 2024
## Grabber
During this session, I modeled, 3d printed, and assembled the grabber. One to tilt the gripper forward and one to open and close the gripper hooks. I use servos because they are very easy to command and very compact compared to their strength. The part that holds the grabber is also used to secure the rail belt. Thera are four screws that go through the belt in order to pinch it so it can not glide off the part.

 

> The upgraded grabber

## Wheels
After a few tests, we found up that the wheels we were using on the robot were not straight at all (buckling of approx. 3 mm) so we ordered some new ones made out of aluminum and rubber arround. After mounting then, I observed that they are almost perfect. Unfortunatelly the wheels are finner than the old one so we have to put two of them in parallel to get the same width.

 

> The new wheels

## Calibration
In order to calibrate the robot's encoder wheels, I modeled in SolidWorks and then laser-cut a plate to fix the robot's center of inertia at a fixed point. This enables the robot to be rotated around a perfectly fixed axis of rotation, and the number of steps taken by each encoder wheel to be counted, so as to check whether or not they are identical, or even to determine a coefficient of divergence between the two. The part is screwed to the robot at both ends, and screwed to a panel on which the robot rolls.



> The robot on the test bench. The part I've added is the light wood part in the middle of the robot.

## Next session
- Design, print and mount the horyzontal rails on the robot.
- Continued progress on ladybug design

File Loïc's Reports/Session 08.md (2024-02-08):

# February 07, 2024
### Vertical rail
Last session, I mounted the vertical rail onto the robot but they looked a bit fragile. I decided reprint them with a thicker wall so they are more robust. Now the vertical rail is strongly attached to the robot, I can fix the stepper motor and the pulley on it. The stepper motor I chose is a pancake Nema 17. It is the same motor as a classic Nema 17 but it is twice as thin and twice as light. The classic version has a torque of **0.26 Nm** but the pancake version has a torque of **0.16 Nm** yet it is enough for the vertical rail which is not supposed to carry a heavy load (a few tens of grams).



> Left: pancake Nema 17; Right: classic Nema 17

 

> The stepper motor is fixed on top of the vertical rail, the pulley is fixed at the bottom of the rail. The belt is around the pulley and the motor shaft and is fixed to the cart of the rail.

### Belt mount
In order to move the cart up and down, a belt is attached to it and turns around the stepper on top of the rail and a pulley at the bottom of the rail. The belt is a GT2 belt, it is a standard belt for 3D printers and CNC machines. The belt is fixed to the cart with a 3D printed part. The part is designed to be fixed to the cart with 4 screws and to hold the belt with 4 other screws which go through the part and the belt. This way, the belt is strongly attached to the cart and the part is strongly attached to the cart.



## 3D modeling
### Ladybug
Now the main robot is almost physically complete, I started to model the ladybugs. These mini robots are designed to pollinate plants picked up within the first 100 seconds by the main robot. To validate this action, every ladybug must move from the departure base to a plant placement area and touch one of the plants.

For the modeling, I used the same process as for the main robot. I started by listing the items a ladybug should carry :
- A lidar or a ultrasonic sensor (to detect the obstacles)
- A Raspberry Pi zero W (Wifi version)
- 2 motors (a DC motor for the motor wheels and a servo motor for the dircetion wheel)
- A battery (Lipo 3.7V 500mAh for its lightness and its small size)
- ...

Then I found on the internet the models of the Raspberry Pi zero and the lidar because they are standard items and it would be a waste of time to model them myself. I have an idea of the size of the motors and the battery we are going to use, so I modeled them myself. Now I have all the models of the main componants, I can start to design the chassis of the ladybug.



> First draft of the ladybug. Ultra compact and light.

## Next session
- Mount the new wheels on the main robot
- Update the grabber's design to fit the vertical rail's belt mount
- Design the main robot's horyzontal rails
- Mount them on the robot
- Model the ladybug's chassis

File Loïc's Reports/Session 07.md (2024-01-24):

# January 23, 2024
## 3D modeling
### Vertical rail mounting
In order to mount the vertical rails, I modeled on SolidWorks two pieces which will hold the rails in place. The first one avoid the rails to move vertically by blocking it at the bottom. It also blocks all the horyzontal translations. The piece is screwed to the base of the robot. The second piece blocks the rails from the rear and blocks the vertical translations thanks to a through screw. It is screwed to the top panel of the robot's frame. The two pieces are shown below in orange.

   

> The two pieces are shown in orange

## 3D printing
### Vertical rail mounting
I printed the two pieces in PETG with a 0.2mm layer height and 50% infill. This settings are the best compromise between printing time and strength. The pieces are shown below in PrusaSlicer.



> The two pieces after slicing

 

> The two pieces after printing

## Laser cutting
### Panels' frame
Since we switched to the U-shaped frame, we made a lot of holes modifiactions. In order to keep our work clean, we decided to laser cut a new frame which includes all the holes we made after the first laser cut. Once the frame was cut, I assembled the robot with the new frame. The frame is shown below.

  

> The new frame and the robot reassembled

### Coding wheels
Last session, I assembled the coding wheels but the springs supposed to keep the wheels in contact with the ground were too strong and their supports were too weak. I made some new ones and I cutted the springs in half in order to reduce their strength.

 

> The new springs and their supports in blue printed plastic

## Next session
- Add to the robot the stepper motor to move the vertical rails.
- Design a grabber that can grab several plants at once.

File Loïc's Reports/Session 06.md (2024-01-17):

# January 16, 2024
### Robot assembly
During this session, finished to assemble the rolling base. It is now ready to be programmed and tested. The next step is to assemble the gripper. We also need to find a way to power the robot. We will probably use a battery pack. For the moment, I am using my home made portable power supply but it is not very convenient and it does not last a long time. I also assembled the coding wheels and the motor encoders. I adjusted the height of the yellow plastic parts to make sure the wheels are touching the ground and that the robot is stable.

  

> The rolling base with my portable power supply on top; a coding wheel mounted onto the rolling base.

### Mecanical power transmission
In order to transmit the power from the motors to the wheels, I chose to use a belts. Last session, I tried to make them myself by sewing the ends of a belt together. During this session, I performed a stress test on the belts by running the motors and pushing the robot against the floor. The belts broke after a few seconds. I then decided to buy some belts online. I found some that are the right size. I will receive them in a few days. I think the problem was the wire I used to sew the ends together. It was too thin and made out of cotton and it broke. Maybe if I had used a thicker wire made out of a stronger material like nylon, it would have worked.



> The belts I bought online.

While testing the belts, I noticed that the belts did not slip on the pulley so I conclued that the system to tension the belts is valid.

## Next session
- Solve the shafts problem
- Add the vertical gripper I made previously

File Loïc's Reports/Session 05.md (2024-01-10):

# January 08, 2024
## Hand made
### Belts
During this session, I sewed the belts for the motorized wheels. The wire provides good tensile strength and the glue prevents the wire from loosening. I used a glue which remains soft after it dries so the assembly stays flexible.

  
> An assembled belt

### Motors mounting holes
After I finished making the two needed belts, I modified the robot frame to make the motors mounting holes oblong. This allows the motors to glide along the frame and adjust the belts tension. Then, I mounted the motors and the wheels with the belts to check if everything was working properly.

 

> A 3D view of the oblong holes I made on the real frame.

### Wheels' shafts
During the last part of the session, I cutted the wheels' shafts to the right length and I tried to thread them but it didn't work because the die was damaged. I planned to thread the ends and then use nuts to stop the shafts axially. I will have to find a new die to finish this task or find another way to stop the shafts.

## Next session
- Solve the shafts problem
- Reassemble the robot entirely
- Add the vertical gripper I made previously
- Add the coding wheels I made previously

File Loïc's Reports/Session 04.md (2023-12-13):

# December 12, 2023
## 3D Modeling
During this session, I modeled on SolidWorks the belt tensioner. To tension the belt, I made oblong holes in the panels of the robot's frame so the motor mounts can translate and by controlling the center to center distance between the two pulleys, I can adjust the tension of the belt.

 

> Belt tensioner

Since I mouved the wheels to the center of the robot, they are no longuer directly mounted on the motor shaft so I had to redesign the hub adapter because the motor's shaft are 8mm in diameter and the wheel's axis only 5mm. Moreover, I would like to transmit the torque from the pulley to the wheel.
I came up with the following design which aims to be pressed into the wheel and goes arround the pulley. Then a screw can be added to avoid a rotation between the wheel and the pulley.



> New wheel hub

To finish, I modeled the encoders mount. I modified the previously made pivot arm which hold the freewheel so the encoder can be mounted on it. The encoders are take from the motor. So I modeled the piece in order to ba able to reuse the encoder's screws.

 

> Encoder mount, the encoder is the green part

## 3D Printing
During the session, I printed the belt tensioner and the wheel hub. I also printed the encoder mount. All pieces are perfect. I chose to print them in PETG because it is stronger than PLA and easy to print.

## Hand Made
I spent a large part of the session to make some holes in the frame of the robot. I forgot a few holes for some screw so I had to make them. It was not difficult because I took the time to take the measures and to mark the holes before drilling them. I also mounted the ball freewheel, the new mounts. I put all the ball bearings into the different parts and the brass inserts as well.

     

> Some photos of the robot from different angles. Plastic protections had not been removed yet. Some screws are missing to save time.

## Next Session
- Cut and thread the shafts
- Finish the frame
- Mount the freewheels (coding wheels)
- Mount the grabber

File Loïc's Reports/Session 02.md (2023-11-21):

# October 21, 2023
## Electronics
The brushless motors we ordered were send with male MT30 connectors which are not convinient for several reasons:
- They are not common so difficult to source at a reasonable price
- They don't allow to swap two phases lines to reverse the rotation direction

Because the ESCs are sold without any connectors, I decided to replace the motors connectors by 3.5mm bullet connectors so we have female connectors on the ESCs and male connectors on the motors. The use of bullet connectors is much more convinient for the reasons mentioned above.

     

Once I finished soldering the connectors, I tested the motors with the ESCs and it worked perfectly. I used a 6S (22V Li-ion) battery to power the ESCs wich are rated for 3S to 6S. I powered the Arduino with the 5V output of the ESC. I mounted the motor on the 3D printed support that will later be used to mount it on the robot.

 

I wrote the following code to test the motors:

```c++
#include <Servo.h>

Servo esc;

int potPin = A0;
int throttle;

void setup() {
  esc.attach(9, 1000, 10000);
}

void loop() {
  throttle = map(analogRead(potPin), 0, 1023, 1000, 10000);
  esc.writeMicroseconds(throttle);
  delay(10);
}
```
My code is really basic, it reads the value of a potentiometer on pin **A0** and writes the value to the ESC using the library ***Servo***. The ESC then sends the corresponding three-phase PWM signal to the motor. The motor speed is proportional to the PWM signal. A video of the test can be found [here](https://github.com/Loic-LEROY/PolyMartian/blob/main/Lo%C3%AFc's%20Reports/src/session_02/run%20test.mp4) on the GitHub repository.

I was really impressed by quality of the motors, they run super smooth and are really quiet.

Here is the whole test setup:



## 3D Modeling
Based on the latest rules given by the cup administrators, we decided to change our strategy. Instead of storing the plants into the robot, we will push all of them in the same time. This way, we don't have to manipulate the plants one by one to put them in the robot. We will directly push them with the robot frame. This will conciderably reduce the time spend to collect the plants.

To match this new strategy, I modeled on SolidWorks a whole new robot. The motorisation remains the same, we still have a grabber to place the plants in the planters. Here is a comparison of the very first version and my first model of the new version:

  

> On the left le first version of the robot, on the right the new version

Before building the new robot, I already found that there is a problem with the new design. The wheels are at an extremity of the robot, so it reduces the maniability of the robot by augmenting the truning radius. To solve this issue, I will have to move the wheels closer to the center of the robot like on the first version. The problem now is that I cannot move the motors from their position because they would block the area where the plants are "stored". The solution is to let the motors where they are and to move the wheels closer to the center of the robot. This will require to use a belt transmission to connect the motors to the wheels. I will also had a belt tensioner to be able to adjust the belt tension.

Here is the new version I come up with:



> Some parts are transparent for a better visibility but they won't be transparent on the real robot.

As you can see on the image above and the images below, I also added one freewheel to each side of the robot. These wheels are not motorised, they aim to measure the distance travelled by the robot. This will allow us to know the position of the robot on the field. I will use a rotary encoder to measure the rotation of these wheels. By measuring the position of the robot on non driving wheels, we ensure that the position is not affected by the slippage of the driving wheels which can append when the robot accelerates or decelerates too much or if it loses traction due to the ground conditions like grease or dust.

   

> Some details of the mounting of the freewheels and the driving wheels.

In order to ensure a good regidity off the mounting of the driving wheels, I added a 3D printed part with a triangular shape for resistance and it creates a great pivot for the driving wheels. More over, I've modelled a system that maintains pressure on the freewheels to avoid distorting the measurements should they come off the ground due to imperfections in the playing surface. This system consists of a swinging arm to which the freewheel is pivotally attached, and which is pressed towards the ground by a spring that forces it to lower the freewheel.

For information, the spring and its support are not yet modeled on the robot model. It will be done next time; all pivot are ball-bearing mounted to reduce friction. All features from the previous version have not been added yet.

## Next time
- Finish the freewhell system
- Model the belt tensioner
- Add the previous features (already modeled for the previous version)

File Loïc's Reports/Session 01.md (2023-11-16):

# October 14, 2023
## 3D modeling
### Wheel adapter
Based on the wheels we ordered from Amazon, I modeled in 3D and 3D printed an adapter to mount them on the motor shafts, as they are sold as rolleur wheels and are therefore freewheels (mounted with a bearing in the hub) and so we can't use them directly to transmit torque from the motor on which they are individually mounted.

  

To make these wheels suitable for our use, I simply removed the bearings from them and replaced them with a 3D printed (in PETG for reliability) adapter that fits the motor shafts. The wheels are then mounted on the motor shafts. In my original design, the adapter was screwed onto the motor shaft, but I had to modify it to make it press-fit because the hole for the screw (in red on the picture above) was not accessible because the wheel covered it. To make sure to have a tight fit, I 3D printed the adapter without any tolerance and I filed it down just a little bit to make it fit just enought to stay in place without risking to damage the motor shafts.

   

In order to transmit the motor torque, I designed the adapter with a flat surface identical to the one on the motor shaft. Because the wheels are only press-fit on the motor shafts, I will have to keep an eye on them to make sure they don't slip. I will have to solve this issue on the next version of the adapter.

   

> We can see a wheel in black, the 3D-printed adapter in white and a motor mounted on a previously-produced 3D-printed bracket, which in turn is screwed onto the laser-cut plywood frame.

### Motor mount
The motors currently in place are DC motors with a planetary gearbox, but we'd like to try brushless motors to see if they're more efficient than DC motors. The brushless motors we have are much larger in diameter but smaller in length, so I had to redesign the motor mount to accommodate them. I also had to redo the spacers between the plywood panels that form the frame, as the brushless motors are too big to fit between the panels.

 

> Both models can be 3D printed without any support so it reduces post processing, material waste and print time.



> On the left the DC motors, on the right the brushless motors.

## Table
We received the game mat that will be put on the 2*3m table. This mat delimits the different action zones in which the robot must move and perform actions determined by the cup rules.
We unwrapped the mat to make sure everything was in order and to see what it looked like. We thought it would be made in a single piece, but it is actually made in 3 pieces that we will have to assemble. We will have to find a way to make the joints between the pieces as invisible as possible.

     

## Next time
I will modify the motors connectors by 3.5mm bullet connectors so we can plug them to the ESCs we received the same day as the mat. 

After that, I will make a quick Arduino code to test the motors and ESCs to make sure everything works as expected.

Then, I will concentrate at the modification of the futur version 3 of the robot to move the wheels to the middle of the chassis and create a system so the motors remain at the rear of the rolling base.



If I have some time left, I will finish the hardware of the grabber system and make a quick Arduino code to test it.

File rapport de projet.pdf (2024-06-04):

LEROY Loïc
WAELES-DEVAUX Adrien

1st year of Master in ‘Robotics and Autonomous Systems’

French Robotics Cup 2024
Project retrospective


Summary:
1. Introduction
2. Electrical diagram
3. Operating algorithm
4. Project costs
5. Problems encountered
6. Conclusion:
a. Accomplishments, functionalities, and issues
b. Next steps
7. Bibliography

Polytech Nice-Sophia
2023-2024

### 1. Introduction

The "Farming Mars with the PolyMartian" project is an initiative developed as part of the Coupe de France de Robotique. This competition, the largest gathering of engineering schools in Europe, focuses on the design and production of autonomous robots capable of completing a series of thematic tasks within a given timeframe. This year's theme is about managing an autonomous greenhouse on Mars, making life possible for astronauts by allowing them to grow fruits and vegetables. To achieve this, our robots must accomplish various tasks: distinguish fragile from resistant plants (5), place them in pots, and release them in their respective planting areas (1, 2, or 7). Additionally, we can earn extra points by swiveling solar panels (8 and 9) to position a part of the vertical projection of the edge with the team color inside the table. Finally, we have the opportunity to develop a swarm of robots that will pollinate plants by touching them in the planting areas, but only during the last 10 seconds of the game. These robots are called the “Ladybugs”.


### 2. Electrical diagram

To power our system, we use two different circuits grounded together. The first one utilizes 2 LiPo batteries in series (2*3s = 24V) for the main circuit below, and the other one involves only one LiPo battery (12V) for the cameras.


### 3. Operating algorithm

To use our robot, we advise proceeding as follows:
1. Position the robot in its starting area.
2. Insert the starter pull cord into its housing.
3. Hold the starter button vertically, keeping as far away from the robot as possible.
4. Turn the emergency stop button to switch on the robot.
5. Wait 15 seconds.
6. Pull the starter grip upwards until it is completely withdrawn from the robot.
7. The robot will start up, following its program.
8. The robot will automatically move to its designated area and stop all movements after 100 seconds. In case of an anomaly, the emergency stop button can be activated at any moment to completely stop the robot.
Be careful! Before switching on the robot, ensure that the batteries are fully charged and placed in fireproof bags. Additionally, never use a battery that is swollen or hot, as this could cause a fire or even an explosion.

### 4. Project costs

To maximize our chances, it was important to work with accurate and reliable components. This often requires the use of professional materials and spare parts to fix unexpected damages or faulty components. To meet our needs, we established sponsorships with various entities that we would like to thank again. We gratefully received funding of up to €8500 from Université Côte d’Azur, our school Polytech Nice-Sophia, Elsys Design, and Sofab Telecom Valley. Additionally, we were extremely fortunate to benefit from a workspace provided by our school, which included a wide variety of tools purchased specifically for our needs.
As we plan to continue developing the association in the coming years and participate in future editions, we did not spend our entire budget this year. Here is our financial account: Robotics Cup registration fee: 200 €
Tools: Total of €600 including a drilling machine, screwdrivers, measurement tools, and more. Sensors and actuators:
- Polymartian (our main robot)
4 JeVois Cameras with processing units included | 2600 €
4 Ultrawide camera lenses | 40 €
1 Nvidia Jetson | 225 €
1 ESP32 | 8 €
2 MD36 DC motors with encoders | 240 €
2 Cytron drivers for DC motors | 36 €
3 Nema17 pancake steppers | 45 €
4 Servomotors 9g with metallic gears | 20 €
6 Ultrasonic sensors | 12 €
8 Lipo 3S 2200mAh | 140 €
1 Charger for LiPo batteries | 45 €
3 Linear guides | 90 €
4 Rubber wheels | 40 €

- Ladybugs (our swarm of 7 robots) :
7 Raspberry Pi Pico W | 105 €
7 DC motors | 78 €
7 Servomotors | 85 €
21 Ultrasonic sensors | 84 €
10 Gyroscope chips | 36 €
10 DWM1001-DEV chips | 190 €
Spare parts:
1 MD36 DC motors with encoders | 120 €
2 Cytron drivers for DC motors | 36 €
2 ESP32 | 16 €
5 Ultrasonic sensors | 10 €
4 Rubber wheels | 40 €
Consumables:
2kg PETG Prusament (for 3D printing) | 60 €
3 Acrylic slabs (used with laser cutting machine) | 90 €
Transportation and accommodation:
Accommodation: Airbnb, 5 nights, 4 students | 400 €
Transport round trip: Highway tolls and gasoline | 500 €
This results in a total of 6191 €. The expenses may seem quite significant for a school project, but most of the materials used will be reused in the following years. This allows our association to reduce expenses progressively while being equipped with a wide variety of tools, motors, and sensors.
Engineer’s salary:
With a total working hour of around 1000, including schoolwork sessions, home development, and day and night work during the competition, if we were to estimate a work price based on a gross salary of €38k for 1600 hours per year, it would require a salary of €23.75k. This significant estimation also accounts for research and development time and commitment to making prototypes.

### 5. Problems encountered

During this project, we encountered several hardware difficulties. We accidentally damaged the USB port on the ESP32 twice, necessitating many hours of repairs to reconnect it to a new board. To enhance circuit reliability and prevent unintentional disconnection, we soldered wires directly to the board.
While working on the coding wheels, we broke a magnet from an encoder. Since this component is not readily available on the market, we had to liaise with the manufacturer to obtain a replacement.
On the software side, we initially struggled to adapt to the ESP32, which operates quite differently from the Arduino due to its 32-bit architecture (compared to Arduino's 16-bit) and dual-core design (compared to Arduino's single core). When training the camera AI, we invested significant time in generating random obstacles to simulate real-world scenarios for the robot.
Determining the PID was also challenging since theoretical coefficients were not readily definable. We adopted a hands-on approach, calibrating the encoder wheels and testing various coefficient combinations before achieving satisfactory results.
During the competition, one of our four cameras exploded due to incorrect specifications provided by the manufacturer. We intend to replace the faulty component to salvage and reuse the camera in the future.

### 6. Conclusion

a. Accomplishments, Functionalities, and Issues During this project, we designed and built a complete autonomous robot. The following functionalities are mechanically fully operational: the rolling base that enables the robot to move, the gripper system mounted on a linear rail that enables the robot to manipulate a particular plant, and the hook system on linear rails that enables the robot to grab a batch of 6 plants in one go and keep them from falling as it moves. On the code side, the AI is functional, although not yet fully implemented on the robot. The robot is able to carry out an autonomous movement sequence thanks to the PID coded on the ESP32. It can also locate and move in space. Finally, the code that manages the use of the linear rails and the actuators mounted on them is not integrated with the rest of the functionalities but works individually.
b. Next steps

This first participation was an incredible experience that allowed us to develop advanced skills in robotics through the realization of a fully autonomous robot. It laid the foundations for future years, as we now have experience to pass on to future participants. As our team plans to return next year, we already have a fully functional rolling base that will only require a few adjustments to align with the next strategy. This will allow us to improve our algorithms even before constructing our rolling base for 2025. Our main focus will be on developing new actuators to meet the tasks outlined in next year's rules and dedicating more time to implementing the robot's decisions.
While our experience with AI and vision technology seems promising, our experience has taught us that it's prudent to simultaneously consider simpler alternatives for next year's challenges. It's often safer to have fewer functionalities that are fully implemented.

### 5. Bibliography

- La-maxi-liste-ressources-eurobot :
- https://github.com/VRAC-team/la-maxi-liste-ressources-eurobot
- Official websites of the robotics cup :
- https://www.coupederobotique.fr/
- https://www.eurobot.org/

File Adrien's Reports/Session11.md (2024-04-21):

# Session report 11: March 05, 2024

**Session objective:** Learn more about PID to enhance our closed-loop control model, implement trapezoidal speed profiles, and conduct research on robot trajectories.

## Research on PID
Previously, I encountered issues with finding the optimum PID coefficients, so I dedicated time to conducting further research. Through this process, I gained valuable insights. All the articles that contributed to these conclusions will be linked in the sources section at the end of the document.

- Firstly, if my motors lack sufficient power to reach the final position, it may be due to the integral coefficient not being large enough. When the error becomes very small, the proportional corrector can struggle to make significant adjustments, as it essentially multiplies a number approaching zero by Kp. In such cases, the only effective correction method is to rely on the integral term, which will see its impact significantly amplified in steady-state.

- I also learned about the importance of selecting the optimal sampling frequency. The sampling frequency determines the interval at which measurements are taken from the encoders and corrections are applied with a PID controller. While it may be tempting to use a very high frequency to increase precision, this approach can lead to inaccuracies. Higher frequencies result in corrections being applied more frequently, but on less precise measurements, as the number of encoder steps measured at the sampling frequency will be lower for the same distance. Conversely, if the sampling frequency is too low, corrections will not be applied regularly enough, resulting in jerky movements.

- Finally, in the context of simple movements such as translations and rotations in robotics, it is common to use trapezoidal speed profiles. These profiles consist of a constant acceleration phase, followed by a phase of constant speed once the maximum speed is reached, and finally, a constant deceleration phase. This approach facilitates smooth movements and helps ensure precise odometry by minimizing slippage.

## Trajectory Planning
There are multiple routes to send the robot from one point to another, so I conducted research to identify the most suitable one for our case.

### 1. Circular Arcs:
The robot follows arcs of circles and straight lines to form a continuous trajectory. While mathematically straightforward, it exhibits C1 discontinuities, which can cause acceleration issues. Additionally, there are risks associated with centrifugal force during high-speed arc changes.

### 2. Bezier Curves:
A promising alternative due to their continuity (C1), but their mathematical complexity poses challenges in path planning. Dismissed due to the difficulties involved.

### 3. Clothoids:
A clothoid is a mathematical curve known for its linear increase in curvature, resembling a spiral shape. It is frequently employed in trajectory planning due to its smooth and continuous curvature changes, offering mechanical advantages, especially in robotics. Opting for a sequence of clothoid arcs ensures a curved trajectory for the robot, helping to avoid acceleration discontinuities and ensuring feasibility.



### 4. Rotation followed by translation
After reviewing robotics cup replays from past years, I observed that most teams opt to avoid curved trajectories due to their complexity. Instead, they choose to use a sequence of independent rotations and translations to reach the desired points. While this approach may not seem optimal, even top-performing teams utilize it and achieve excellent results because it minimizes errors in position and centrifugal problems. Additionally, since distances to travel are relatively short in this competition, the difference in time between this method and previous ones is negligible. Therefore, considering the limited time remaining before the competition (only 2 months), I have decided to adopt this method for this year.

## Trapezoidal speed command
I dedicated the end of the session to researching how to implement a trapezoidal speed command to prevent wheel spinning both at the start and end of the robot's movement, ensuring that the setpoint is not exceeded. I explored various algorithms before selecting the most accurate and easy-to-implement method. Drawing from the experience of the Cubot Team, who generously shared their insights on their GitHub repository, I learned that this can be achieved by calculating the duration of each phase using kinematic equations, along with parameters such as maximum allowed speed, acceleration, deceleration coefficients and the target distance. With these durations determined, we can then determine the appropriate speed to send to each motor to reach the desired position throughout the three phases.

## **Next session tasks:**
In the upcoming session, I will implement trajectories to navigate coordinates and reach any point on the table. Additionally, I will simultaneously implement the trapezoidal speed profile.

## Sources :
https://github.com/VRAC-team/la-maxi-liste-ressources-eurobot/blob/master/asservissement/totofweb-PID_r%C3%A9gulation_de_position_vitesse.pdf

https://github.com/VRAC-team/la-maxi-liste-ressources-eurobot/blob/master/asservissement/TechTheTroll-trajectoire_courbe.pdf

https://github.com/VRAC-team/la-maxi-liste-ressources-eurobot/blob/master/asservissement/Cubot-atelier_asservissement.pdf

Cloithoid image from : https://en.wikipedia.org/wiki/Euler_spiral

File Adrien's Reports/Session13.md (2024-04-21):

# Session report 13: March 19, 2024

**Session objective:** Implement the equations from the previous session in an algorithmm to allow displacements following speed profiles.

I implemented the speed profile from the previous session divided in two main functions :

# Get_speed_target() 
This function takes in entry the remaining distance to travel, and the distance to travel during both constant speed and deceleration phases and returns speed_target, the speed we want the robot to reach.
It will be called each time before applying PID so depeding on the sample frequency.

An enum variable indicates the current speed phase which can be STATIONARY, ACCELERATION, CONSTANT_SPEED or DECELERATION.

Here is how it works : 
1) STATIONARY phase : 
When we receive a new command we switch from STATIONARY to ACCELERATION phase.
2) ACCELERATION phase : 
We simply add the maximum acceleration to the speed target. Execept when the remaining travel distance becomes inferior to the sum of deceleration and constant_speed phase distances where we will have to switch the enum to CONSTANT_SPEED phase.
3) CONSTANT SPEED phase : 
In this new phase, speed_target will remain constant to the maximal speed until the remaining distance turn below deceleration distance which implies to switch to DECELERATION PHRASE
4) DECELERATION phase :
We add the maximum deceleration (which is negative) to speed_target until reaching a value close to zero defined by a variable called precision. When the remaining distance is below the wanted precision, we can stop the robot with speed_target = 0 and switch to STATIONARY. Therefore we will avoid correcting error during a too long period of time to not loose too much time during the competition.

# Get_phases_distance()
This function is called one time after each new command and returns the distances to travel during the three trapezoidal phases depending on the following parameters : distance_setpoint, max_acceleration, max_deceleration and max_speed.

The main difficulty was due to roundings when proceeding to divisions, indeed due to our encoders which have a finite number of points, we have a limited precision so we need to round our numbers to integers. Therefore when the distance value was rounded up the robot was exceeding the target.

So a tip is to round all divisions down with the floor() function and then reduce numerical errors with the following procedure.

1) First, we calculate the acceleration_time, deceleration_time, acceleration_distance, deceleration_distance using the formulas determined in the previous report.
2) If acceleration_distance + deceleration_distance is inferior to distance_setpoint, then we have to recalculate the deceleration distance to fit with a triangle speed profile (see formula from previous report). Thus we have to calculate the maximal speed reached which is equal to the new deceleration_time multiplied by max_deceleration.
3) Then we deduce the constant speed phase duration which is : 
    - equal to zero, in a triangle speed profile
    - equal to the distance_setpoint minus acceleration and deceleration distance, in a trapezoidal speed profile
4) Last but not least, we reduce numerical errors by recalculating the deceleration_distance with our new informations and this time without division so we reduce rounding error : 
$$ deceleration_distance = distance_setpoint - max_speed*constantspeed_time - acceleration_distance $$

## Next session tasks
Finish the whole new closed loop control algorithm including speed profiles displacements to test it on our playing table.

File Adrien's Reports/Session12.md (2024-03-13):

# Session report 12: March 12, 2024

**Session objective:** Develop equations to implement a trapezoidal speed profile for our robot and determine the absolute position of the robot.

# Trapezoidal speed profile

To achieve smooth acceleration and braking, thus preventing slippage, we can implement speed control using a trapezoidal speed profile characterized by three phases: acceleration, constant speed when the maximum authorized speed is reached, and deceleration. I have modeled the profile on GeoGebra to gain a better understanding of the required actions.

[My geogebra modelisation : https://www.geogebra.org/m/n7wgewmr](https://www.geogebra.org/m/n7wgewmr)



Firstly, we can calculate the duration of the acceleration phase and the deceleration phase using our data.

$$ accelerationTime = maxSpeed / maxAcceleration $$
$$ decelerationTime = maxSpeed / maxDeceleration $$

Now, we can deduce the distance traveled during these durations using the kinematic equation for uniformly accelerated motion, which is: 

$$Displacement = InitialPosition+ \frac{1}{2} * Acceleration * t^{2}$$

Thus :
$$accelerationDistance = \frac{1}{2} \cdot \text{maxAcceleration} \cdot \text{accelerationTime}^{2}$$
$$decelerationDistance = \frac{1}{2} \cdot \text{maxDeceleration} \cdot \text{decelerationTime}^{2}$$

If $(accelerationDistance + decelerationDistance) < \text{commandDistance}$,  we can apply this profile; otherwise, we won't have enough time to execute the constant speed phase and will proceed with a triangular speed profile.

Finally, we can calculate the distance to be covered during the constant speed phase:

$$constantspeedDistance = \text{commandDistance} - accelerationDistance - decelerationDistance$$

Therefore :

$$constantspeedTime = \frac{constantspeedDistance}{\text{maxSpeed}}$$

We are now almost ready to implement this profile in our robot. However, there are additional steps required to reduce rounding errors, but we will address those in the next session.

# Triangle speed profile
Sometimes, the distance command may not be large enough to accommodate the entire trapezoidal speed profile, as we might not have sufficient time to reach the maximum speed. In such cases, we will need to forego the constant speed phase and proceed directly to the acceleration and deceleration phases, resulting in a triangular speed profile.

The main challenge in implementing this triangular profile is that, unlike before, we do not know the maximum speed we will be able to reach. Therefore, I had to find a formula to determine the deceleration duration of this triangular speed profile, considering only the maximum acceleration and deceleration and the distance to be traveled.

To better understand the problem, I modeled it in GeoGebra, so you can visualize it below, where $\tau$ represents the deceleration time we are searching for:

[My geogebra modelisation : https://www.geogebra.org/m/q3h9c6sb](https://www.geogebra.org/m/q3h9c6sb)



We define the following variables : 

Known variables : 
- $a_1$ : maximum acceleration of the robot,
- $a_2$ : maximum deceleration of the robot (negative value),
- $v_2$ : robot's speed at the end of the deceleration phase (= 0 cause at the end of deceleration the robot shouldn't be moving),
- $d_2$ : total distance command.

Unknown variables : 
- $v_1$ : robot's speed at the end of the acceleration phase,
- $t_1$ : time to complete the acceleration phase,
- $t_2$ : time to complete the whole speed profile,
- $d_1$ : distance to perform acceleration phase.

Then we can formulate the following equations from the problem:

$$
\begin{cases}  
v_1 = a_1 \cdot t_1 \\ 
v_2 = a_2 \cdot (t_2 - t_1) + v_1 = 0 \\ 
d_1 = \frac{1}{2} \cdot a_1 \cdot t_1^{2} \\ 
d_2 - d_1 = \frac{1}{2} \cdot a_2 \cdot (t_2 - t_1)^{2} + v_1 \cdot (t_2 - t_1) 
\end{cases}
$$

We have 4 unknown variables and 4 equations, therefore we should be able to solve this system.

For better readability, let's define $$\tau = t_2 - t_1$$ as the unknown we are searching for.

$$\Leftrightarrow \begin{cases} 
v_1 = a_1 \cdot t_1 \\ 
v_2 = a_2 \cdot \tau + v_1 = 0 \\ 
d_1 = \frac{1}{2} \cdot a_1 \cdot t_1^{2} \\ 
d_2 - d_1 = \frac{1}{2} \cdot a_2 \cdot \tau^{2} + v_1 \cdot \tau 
\end{cases}$$

Now let's solve this system : 

$$ l_2, l_3 \rightarrow l_4 \implies d_2 - \frac{1}{2} * a_1 * t_1^{2} = \frac{1}{2} * a_2 * \tau^{2} + (-a_2 * \tau) * \tau $$

$$ \Leftrightarrow d_2 = -\frac{a_2}{2} * \tau^{2} + \frac{a_1}{2} * t_1^{2} $$

$$ l_1, l_2 \implies a_1 * t_1 = v_1 = -a_2 * \tau $$

$$ \implies d_2 = -\frac{a_2}{2} * \tau^{2} - \frac{a_2}{2} * \tau * t_1  $$

$$ \Leftrightarrow d_2 = -\frac{a_2}{2} * (\tau^{2} + \tau * t_1)  $$

$$
\Leftrightarrow \begin{cases} 
(a_1 + a_2) \cdot \tau - a_1 \cdot t_2 = 0 \\ 
\frac{a_2}{2} \cdot t_2 = d_2 
\end{cases}
$$

$$
\Leftrightarrow \begin{cases} 
t_2 = \frac{a_1 + a_2}{a_1} \cdot \tau \\ 
\frac{a_2}{2} \cdot \tau \cdot t_2 = d_2 
\end{cases}
$$

$$ l_1 \rightarrow l_2 \implies d_2 = \frac{a_2}{2*a_1} * (a_1 + a_2) * \tau^{2} $$

$$\tau = \sqrt{ \frac{2d_2a_1}{a_2(a_1+a_2)} }$$

If necessary, we can also determine the maximum speed $v_1$ now.

$$ v_1 = a_2 * \tau $$

Important note: In our calculus, we considered $a_2$ as a negative value.

# Determining the absolute position of the robot
I have also incorporated basic calculus into my code to track the absolute position of the robot. Each time I sample my measurements, I calculate the distance traveled in centimeters and the angle traveled in radians during this short period. I then update three variables, X, Y, and Z, with basic trigonometry relations to represent the position. Here's how it works:

$$ Z_{position} = Z_{previousposition} + angle_{travelled} $$
$$ X_{position} = X_{previousposition} + (distance_{travelled} * cos(Z_{position})) $$
$$ Y_{position} = X_{previousposition} + (distance_{travelled} * sin(Z_{position})) $$

And $Z_{position}$ will always be reduced to a value between $-2*\pi$ and $2*\pi$ 

Thus, I am able to obtain the absolute position of the robot on the table in real-time, regardless of its trajectory.

## Special thanks
I would like to thank Mr. Florian Sylvestre, a former Eurobot participant, who took the time to explain in detail how to combine speed profiles and PID, and my mechanical teacher, Mr. Franck Pluvinage, who helped me with kinematic theory.

## Next session tasks
Implement these speed profile equations into my algorithm and estimate the virtual position of the robot resulting from a command sent. Compare it with the real position obtained and correct any errors using PID.

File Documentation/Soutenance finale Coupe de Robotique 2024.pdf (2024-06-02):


# COUPE DE FRANCE DE ROBOTIQUE 2024

### POLYTECH NICE SOPHIA

### ROBOTIQUE ET SYSTÈMES AUTONOMES


01

La compétition

02

### Nos robots

03

### Stratégie et évolution

04

### Solutions mécaniques

05 06

### Déplacements et localisation

07 08

### Retour d’expérience

### Calcul de trajectoires

### IA & Vision

# NOTRE ÉQUIPE


# 1 - LA COMPÉTITION


# LES MISSIONS DU POLYMARTIEN

Orienter les panneaux solaires; Retourner recharger ses batteries; Estimer le score obtenu

Ramasser des plantes
et les mettre en pot

Éviter le robot
adverse

Identifier les plantes

# 2 - NOS ROBOTS


Polymartian
Robot principal

LadyBots
Essaim de 6 robots

# 3 - STRATÉGIE ET ÉVOLUTION



# SOLUTION RETENUE

> Robot en forme de U

> Pousser les plantes par lot de 6

> Rapidité maximale

> Optimisation des déplacements

# 4 - LES SOLUTIONS MÉCANIQUES


Pince multiaxe sur rail linéaire

Roues codeuses : précision, fiabilité

Châssis en PLEXIGLASS superposé : rigide, léger, pratique

# LE POLYMARTIAN


# 5 - DÉPLACEMENTS ET LOCALISATION


Profil trapézoidal de vitesse

4) Position réelle
5) Calcul d’erreurs
6) PID

1 ) Calcul durée des 3 phases
2) Vitesse de chaque roue
3) Position théorique du robot


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

# 7 - IA ET VISION

> 4 caméras, lentilles fisheyes > Équivalentes à 65 Jetson Nano > Vision panoramique à 360°
> IA embarquée et précalculée
> Données analysées par la carte Nvidia > Analyse du terrain 10x par seconde

# 8 - RETOUR D’EXPÉRIENCE

Difficultés techniques; Résultats; Robot homologué; 31points en 1 match; Explosion d’une caméra à 600€; ESP32 non fonctionnel; Compatibilité électromagnétique; Budget; Subventions : 5700€ Sponsoring : 1000€ Total : 6700€

> Privilégier les solutions simples
> Fixer des échéances
> Plus de polyvalence au sein de l‘équipe

# 8 - RETOUR D’EXPÉRIENCE

Budget; Difficultés techniques; Résultats; Robot homologué; 31points en 1 match; 69ÈME / 200 ÉQUIPES; Explosion d’une caméra à 600€; ESP32 non fonctionnel; Compatibilité électromagnétique; Subventions : 5700€ Sponsoring : 1000€ Total : 6700€

> Privilégier les solutions simples
> Fixer des échéances
> Plus de polyvalence au sein de l‘équipe


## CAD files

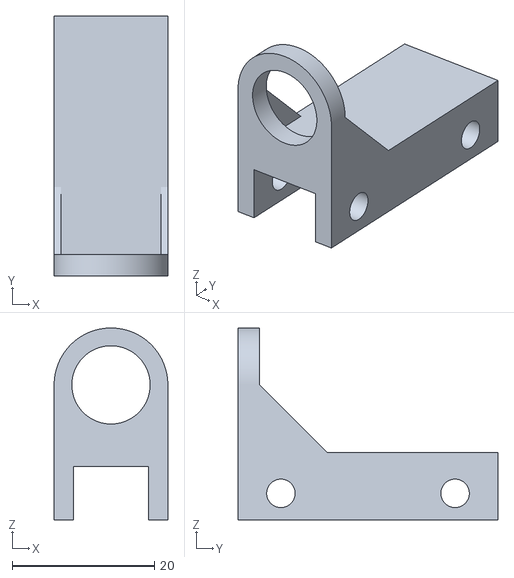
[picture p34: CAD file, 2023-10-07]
Fabrication/Impressions 3D/support roulement.STL
16.0 x 36.5 x 27.0

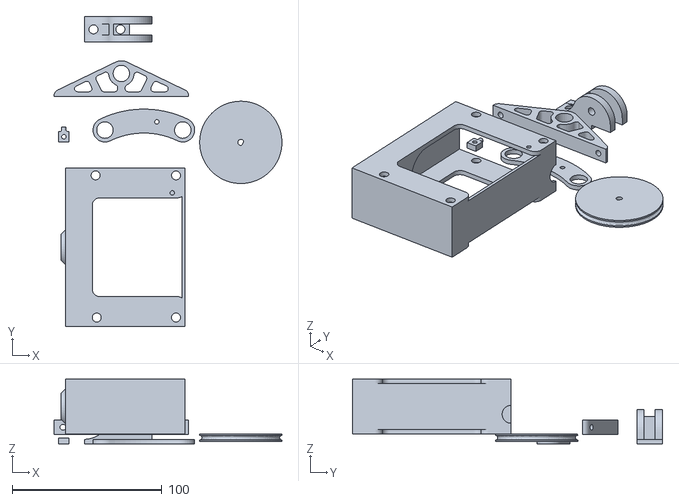
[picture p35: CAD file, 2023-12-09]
Loïc's Reports/src/session_03/support pivot.stl
152.3 x 207.2 x 43.2

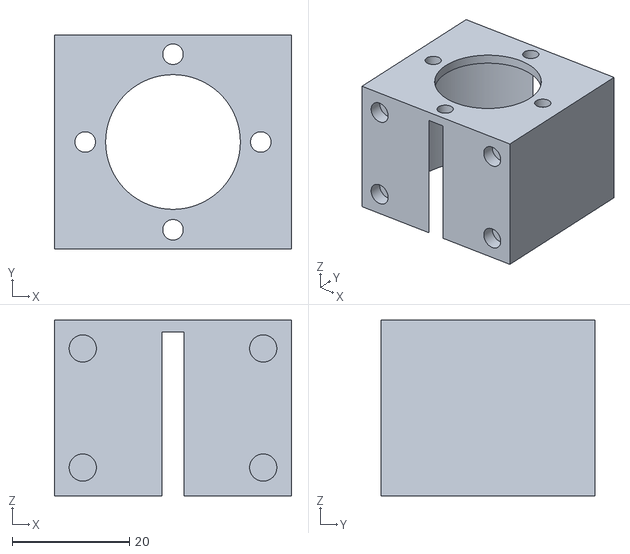
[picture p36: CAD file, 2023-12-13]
Loïc's Reports/src/session_04/support moteur + tendeur.STL
40.5 x 36.5 x 30.0

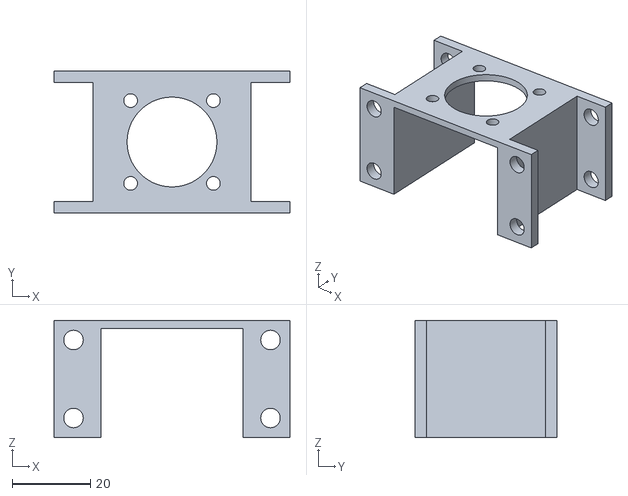
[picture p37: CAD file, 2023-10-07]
Fabrication/Impressions 3D/support moteur.STL
60.5 x 36.5 x 30.0

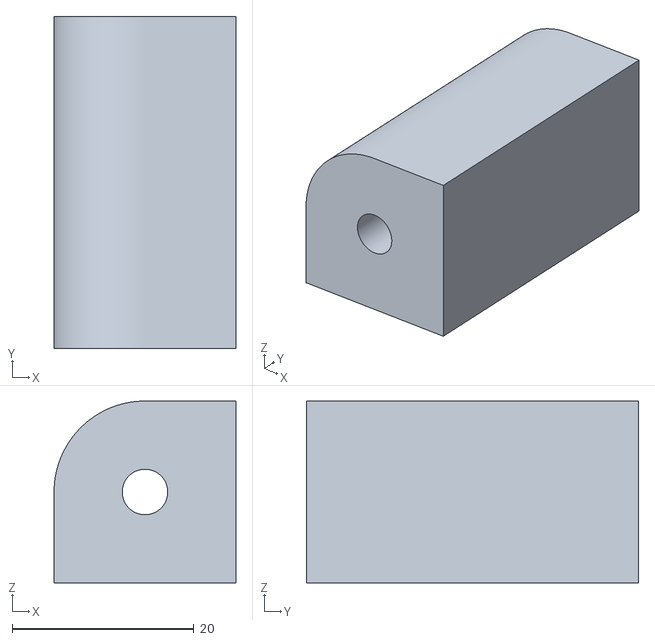
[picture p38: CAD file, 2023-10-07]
Fabrication/Impressions 3D/coin.STL
20.0 x 36.5 x 20.0

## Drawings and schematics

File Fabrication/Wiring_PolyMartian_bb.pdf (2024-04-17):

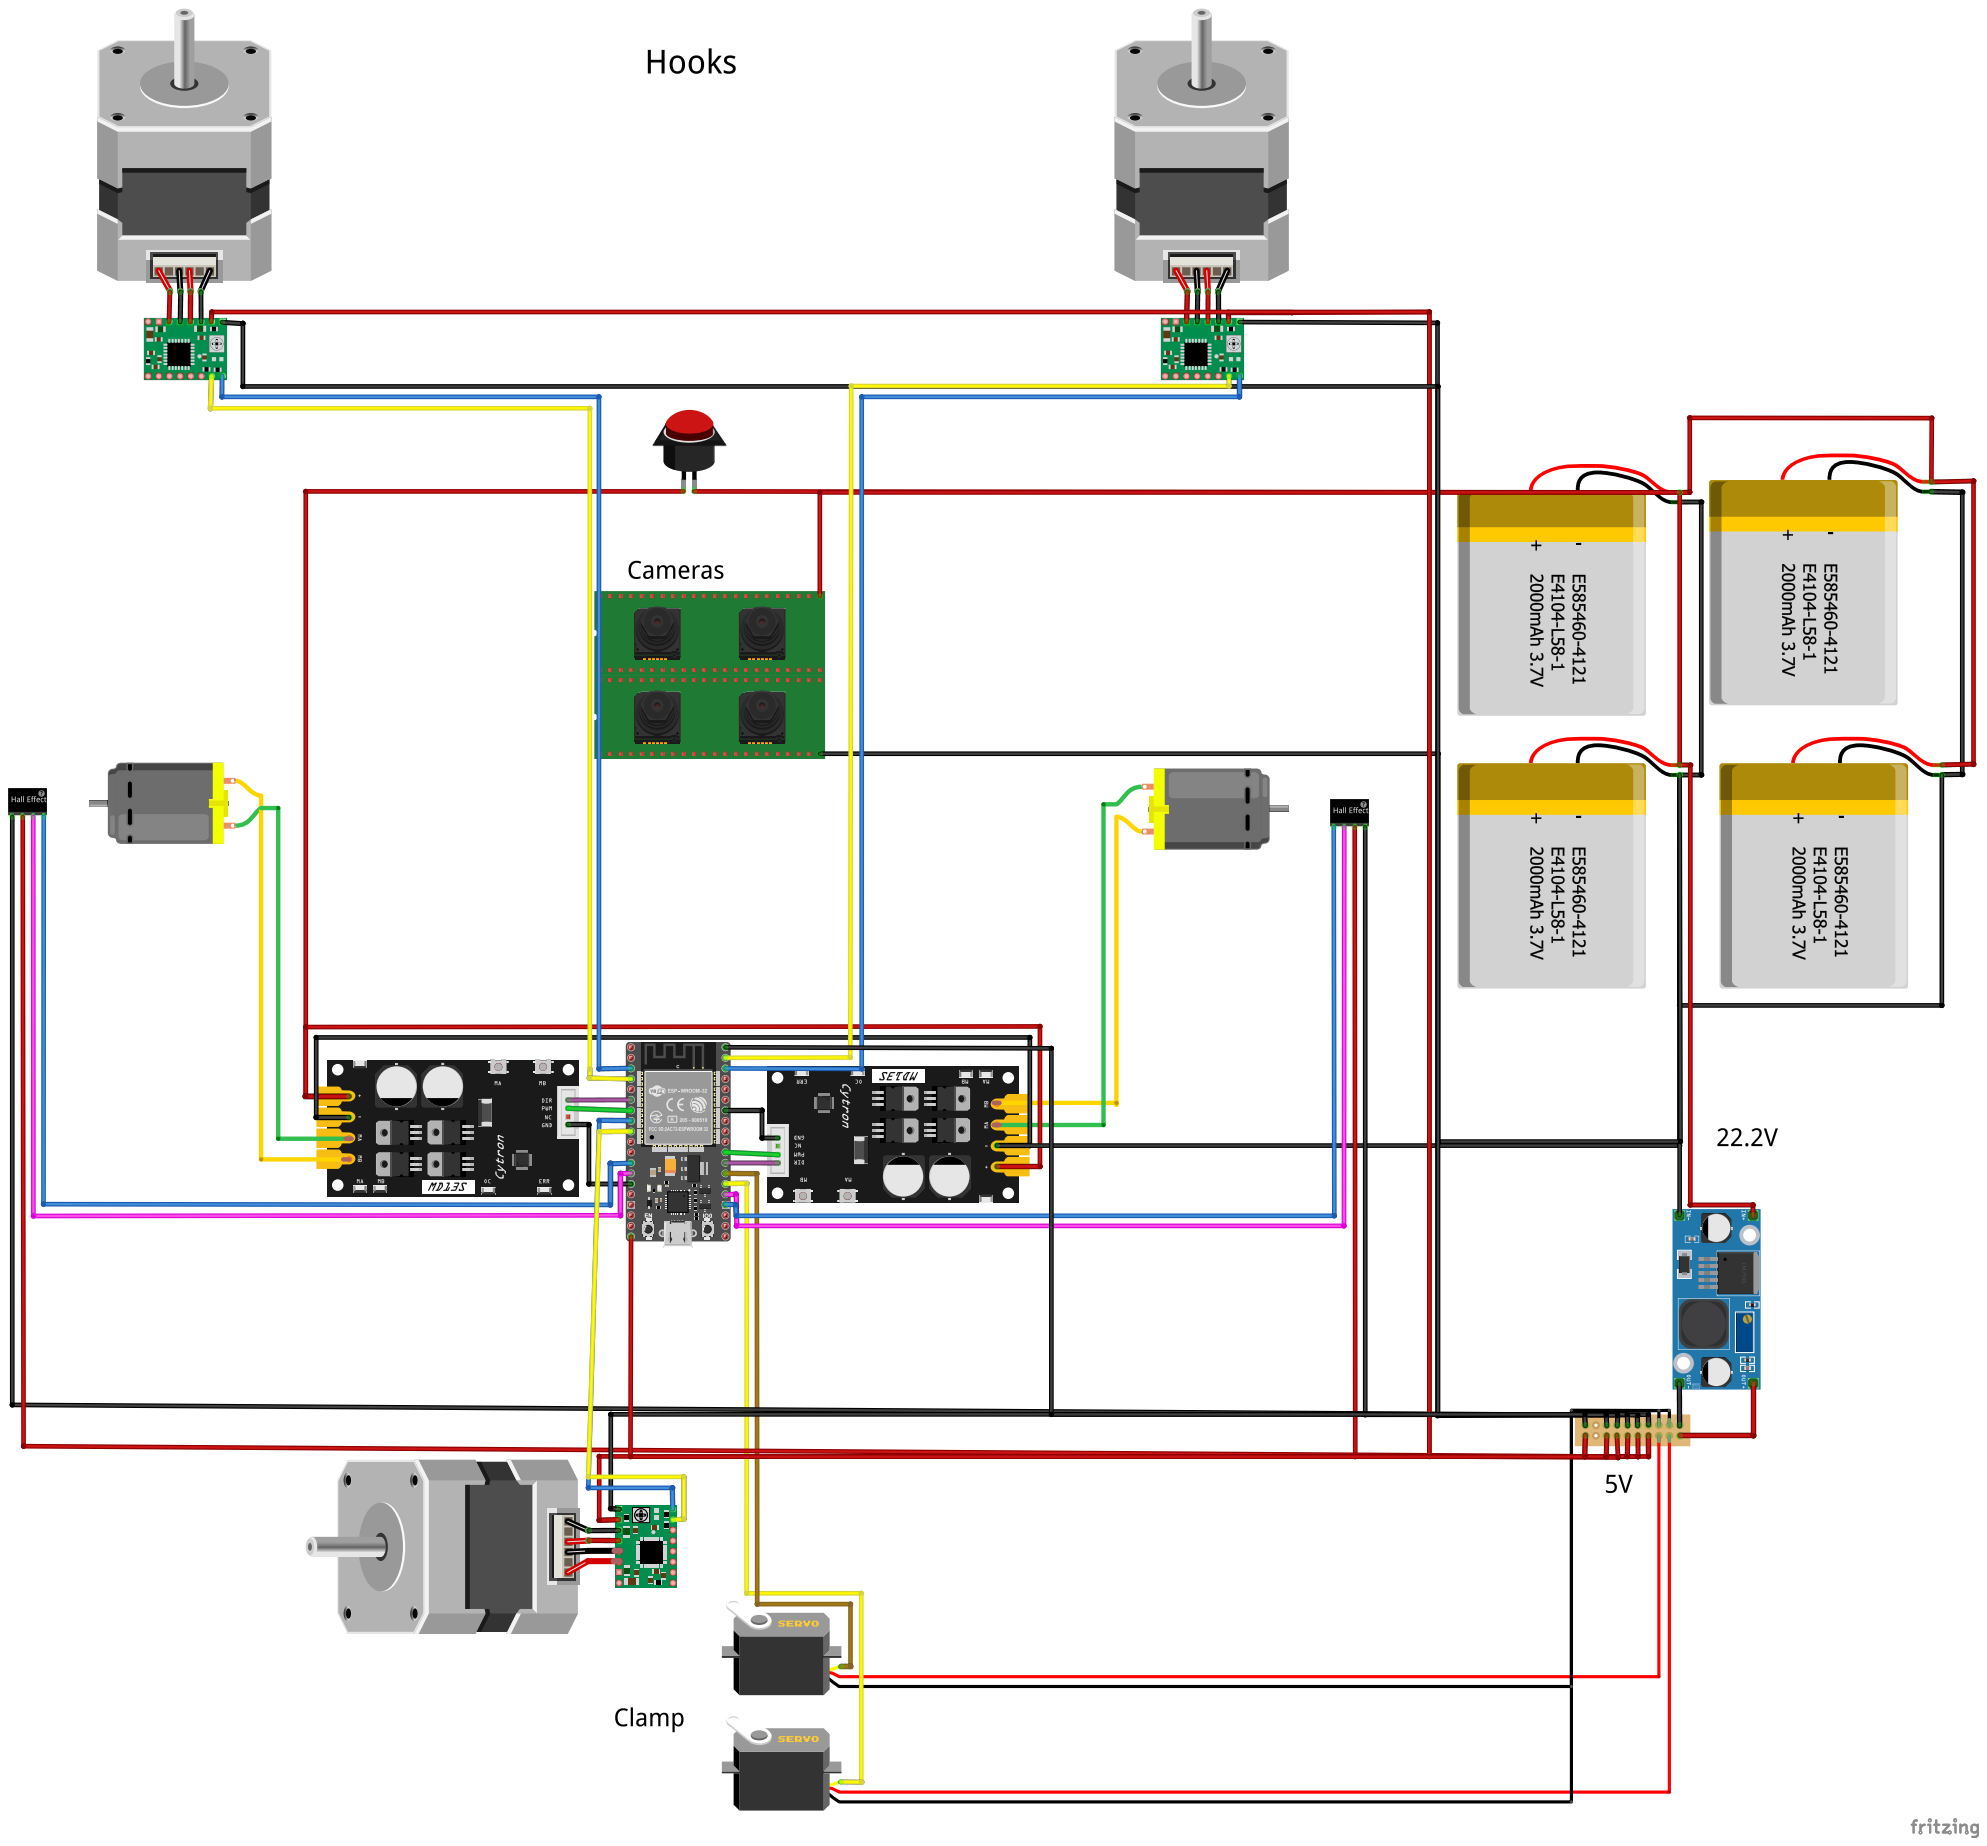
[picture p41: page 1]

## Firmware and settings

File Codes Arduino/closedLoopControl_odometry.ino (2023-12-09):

// MOTORS
#define L_MOTOR 6 // left motor
#define L_MOTOR_DIRECTION 7 // rotation direction of left motor
#define R_MOTOR 8 // right motor
#define R_MOTOR_DIRECTION 9 // rotation direction of right motor

//ENCODERS
#define L_ENCODER_A 2 // left encoder
#define L_ENCODER_B 4
#define R_ENCODER_A 3 // right encoder
#define R_ENCODER_B 5

#define L_ticks_perCm 50 // number of ticks (points) read by the left encoder per cm travelled
#define R_ticks_perCm 50 // same for right encoder

// Trigonometric direction rotation
#define L_trigo_ticks_perRad 1000 //  number of ticks (points) read by the left encoder processing a 1 radian rotation in trigo direction
#define R_trigo_ticks_perRad 1000 // by the right encoder

// Clockwise rotation
#define L_clockwise_ticks_perRad 1000 // number of ticks (points) read by the left encoder processing a 1 radian rotation in clockwise direction
#define R__clockwise_ticks_perRad 1000 // by the right encoder

long L_encoder_ticks = 0;
long L_encoder_previous_ticks = 0;
long L_encoder_deltaTicks =  0; // number of ticks measured by the left encoder after a short time
float L_angle_travelled_rad = 0; // angle travelled by the left wheel in radians

long R_encoder_ticks = 0;
long R_encoder_previous_ticks = 0;
long L_encoder_deltaTicks =  0; // number of ticks measured by the right encoder after a short time
float R_angle_travelled_rad = 0; // angle travelled by the right wheel in radians

float distance_travelled_cm = 0; // distance in cm travelled by the robot after a short time
float angle_travelled_rad = 0; // angle travelled by the robot in radians

float L_integral_error = 0;
float R_integral_error = 0;
float L_previous_speed_error = 0;
float R_previous_speed_error = 0;

float L_command;
float R_command;
float distance_command_cm;
float angle_command_rad;

float speed_coeff = 1; // Factor to convert the speed measured to a number between 0 et 255 (so we will be able to compare it with our command)

// PID coefficients
float P = 0.5; // PID proportional coefficient
float I = 0.5; // PID integrating coefficient
float D = 0.0; // PID derivative coefficient

unsigned long previousmillis = 0; // Last measured time


void setup() {
  //MOTORS
  pinMode(L_MOTOR, OUTPUT);
  pinMode(L_MOTOR_DIRECTION, OUTPUT);
  pinMode(R_MOTOR, OUTPUT);
  pinMode(R_MOTOR_DIRECTION, OUTPUT);

  //ENCODERS
  pinMode(L_ENCODER_A, INPUT_PULLUP); // INPUT_PULLUP so if there is no signal on this pin, we will receive the value 1, so when we will reveive something it will be 0
  pinMode(L_ENCODER_B, INPUT_PULLUP);
  pinMode(R_ENCODER_A, INPUT_PULLUP);
  pinMode(R_ENCODER_B, INPUT_PULLUP);

  // ENCODERS Interruptions
  // The macro CHANGE triggers an interrupt when the pin changes, whether from LOW to HIGH or HIGH to LOW
  attachInterrupt(digitalPinToInterrupt(L_ENCODER_A), L_Encoder_interrupt, CHANGE); 
  attachInterrupt(digitalPinToInterrupt(R_ENCODER_A), R_Encoder_interrupt, CHANGE);

  //SERIAL COMMUNICATION
  Serial.begin(9600); // speed of communication
}

void motors_command(float L_command, float R_command){ // L_command and R_command between -255 and 255 (if negative the wheel goes backward)
  if (L_command>=0){
    digitalWrite(L_MOTOR_DIRECTION, LOW);
  }
  else{
    digitalWrite(L_MOTOR_DIRECTION, HIGH);
  }
  if (R_command>=0){
    digitalWrite(R_MOTOR_DIRECTION, LOW);
  }
  else{
    digitalWrite(R_MOTOR_DIRECTION, HIGH);
  }
  analogWrite(L_MOTOR, abs(L_command));
  analogWrite(R_MOTOR, abs(R_command));
}

void L_Encoder_interrupt(){ // called when there is an interruption on the left encoder pin A
  // L_ENCODER_A and L_ENCODER_B are the same signal but are out of phase. We defined the interruption on the L_ENCODER_A pin
  if (digitalRead(L_ENCODER_A)==digitalRead(L_ENCODER_B)){ 
  // So if the previous condition is true, it means that when the pin L_ENCODER_A detected a high value and interrupted the programm, the B pin was already detecting a high value
  // So the first signal to have a high value was the L_ENCODER_B, with our configuration it means the wheel is moving forward.
    L_encoder_ticks ++;
  }
  else{ // else the wheel is moving backward
    L_encoder_ticks --;
  }
}


void R_Encoder_interrupt(){ // called when there is an interruption on one of the right encoder pin
  // same explanation as left interrupt function
  if (digitalRead(R_ENCODER_A)==digitalRead(R_ENCODER_B)){ // the wheel is moving forward
    R_encoder_ticks ++;
  }
  else{ // the wheel is moving backward
    R_encoder_ticks --;
  }
}

void loop() {

  if (millis()-previousmillis>100){ // we measure the number of ticks every 100 milliseconds
    previousmillis = millis();

    L_encoder_deltaTicks = L_encoder_ticks - L_encoder_previous_ticks;
    R_encoder_deltaTicks = R_encoder_ticks - R_encoder_previous_ticks;
    L_encoder_previous_ticks = L_encoder_ticks;
    R_encoder_previous_ticks = R_encoder_ticks;

    distance_travelled_cm = (L_encoder_deltaTicks/L_ticks_perCm + R_encoder_deltaTicks/R_ticks_perCm)/2; // Distance travelled = average of distance travelled by each coding wheel

    if (L_encoder_deltaTicks>0){ // if the left wheel turns in trigonometric direction
      L_angle_travelled_rad = L_distance_travelled_cm/L_trigo_ticks_perRad;
    }
    else{ //clockwise direction
      L_angle_travelled_rad = L_encoder_speed/L_clockwise_ticks_perRad;
    }

    if (R_encoder_deltaTicks>0){ // if the right wheel turns in trigonometric direction
      R_angle_travelled_rad = R_encoder_speed/R_trigo_ticks_perRad;
    }
    else{ //clockwise direction
      R_angle_travelled_rad = R_encoder_speed/R_trigo_ticks_perRad;
    }

    angle_travelled_rad = (R_speed_error - L_speed_error)/2; // Angle travelled = average of angle travelled by each coding wheel (the two wheels turn in the opposite direction so there is a minus sign)

    distance_command_cm -= distance_travelled_cm; // Remaining distance to achieve
    angle_command_cm -= angle_travelled_rad; // Remaining angle to achieve

    
    //L_integral_error += L_speed_error;
    //L_command = P*L_speed_error + I*L_speed_error + D*(L_speed_error-L_previous_speed_error); //PID correction

  }
  
 

}

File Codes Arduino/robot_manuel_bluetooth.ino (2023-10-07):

//variable encodeur
#define ENCODER_PIN 2
#define ENCODER_N   20
unsigned long T1 = 0, T2 = 0, T;
bool MeasDone = 0;
int Motor_RPM = 0;
//variable bluetooth
#include<SoftwareSerial.h>
#define RX 6
#define TX 11
#define LED 9
SoftwareSerial BlueT(RX,TX);
char Data;
//variable moteur
int mot1 = 3;
int mot2 = 5;
//int cod1 = 10;
int cod2 = 2;
int commande = 255;
int mesure;

void INT0_ISR(void)
{
  if(MeasDone)
  {
    T2 = micros();
    T = T2 - T1;
    MeasDone = 0;
  }
  else
  {
    T1 = micros();
    MeasDone = 1;
  }
}

void setup() {
  pinMode(mot1, OUTPUT);
  pinMode(mot2, OUTPUT);
  //pinMode(cod1, INPUT);
  pinMode(cod2, INPUT);
  //Serial.begin(9600);
  BlueT.begin(9600);
  attachInterrupt(digitalPinToInterrupt(ENCODER_PIN), INT0_ISR, RISING);
}

void loop() {
  if (BlueT.available()){
    Data=BlueT.read();
  if (Data=='A') {
    commande = BlueT.parseInt();
    //Serial.println(commande);
    }
  }

  Motor_RPM = (60000000) / (T * ENCODER_N);
  //Serial.print("Motor RPM: ");
  //Serial.println(Motor_RPM);

  mesure = Motor_RPM*0.047;
  analogWrite(mot2, commande);
  analogWrite(mot1, mesure);
  //Serial.println(mesure);
}

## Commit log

2023-10-08 Création des dossiers de rapport
2023-12-09 session 03
    [support pivot.stl]
2023-12-13 session 04
    [support moteur + tendeur.STL]
